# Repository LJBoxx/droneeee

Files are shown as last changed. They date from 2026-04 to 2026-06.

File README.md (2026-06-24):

# RP2350 Flight controller stack 

This repo contains the design files for a rp2350 based flight controller stack, with an [am32](https://wiki.am32.ca/development/Hardware-Design.html) based 4-in-1 modulable esc.
The esc part is split onto 3 boards : 
- top and bottoma board with logic and mosfet drivers (logic)
- middle with mosfets and power converters (powerstage)

This design allows for repairability, if you want to change the power board for a higher current one or if you have burnt it, just swap it out and solder a new board ! 

I also wanted to experiment with the newly supported rp2350 mcu on betaflight ! Madflight has an esc but I haven't seen any on a 30.5x30.5 "classic" format yet.

Thhe flight controller is quite simple and only has support for the essential to fly digital fpv with : 
- uart for elrs/radio transceiver 
- uart for video like openipc or dji
- uart for gps (additionnal too!)
- one spare i2c port (because there was room for it :v)
- power (9v 3a max, 5v 3a max and 3v3 200ma max **only use if necessary**)

Additionally, there are also some betaflight rgb headers and buzzer. Since it is an rp2350 with PIO, it should be easy to repurpose the i2c port for something else. The pinout is also similar to the madflight fc3 but not exactly the same, in /src/firmware/betaflight/picoflight/config.h you will find the exact files needed to build a firmware along precompiled binary 

At first i wanted to make an esc to work with Alice's flight controller but in the end, i started changing some parts like power converters, removing analog parts and tried to overall optimize the design. In the end it wasnt the same anymore. I also wanted to experiment with the rp2350 as no flight controller exist yet with it. One more thing was trying to make even more compact designs than before, high density layout is fun but also a pain lol.. 

## Renders :
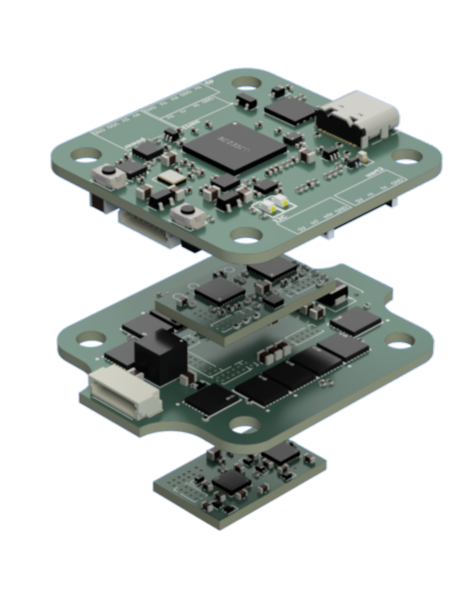
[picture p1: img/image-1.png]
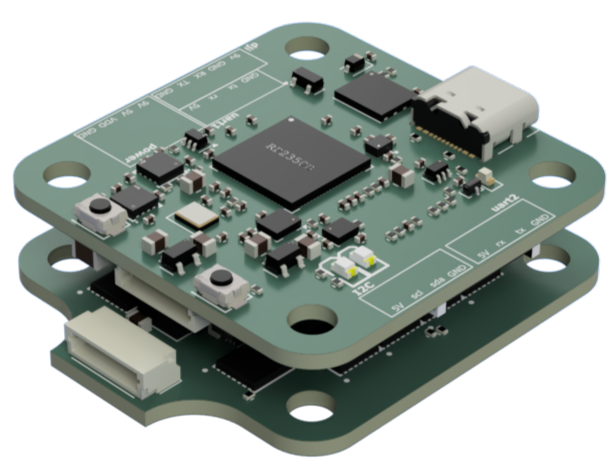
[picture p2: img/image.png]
 

## Schematics 
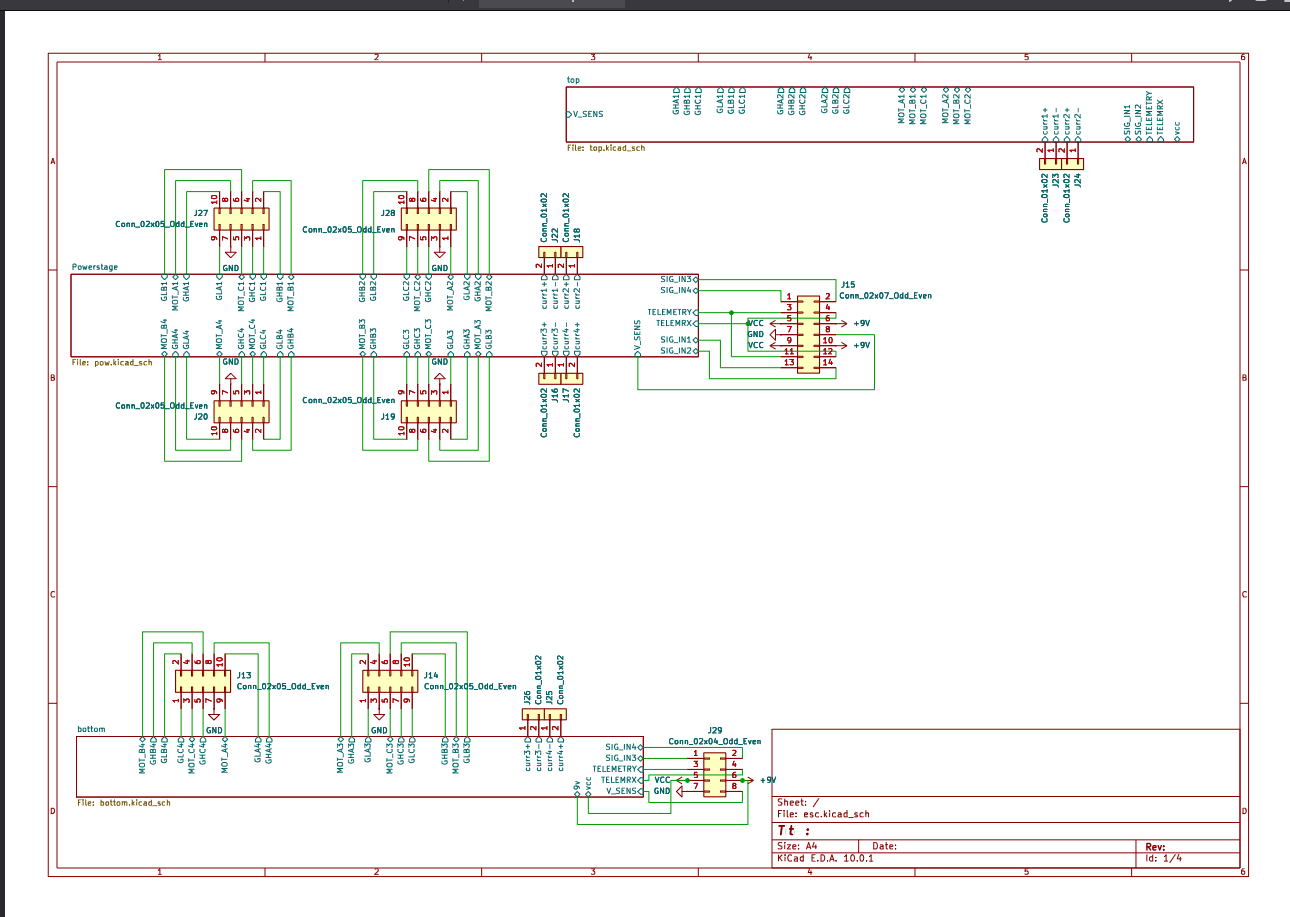
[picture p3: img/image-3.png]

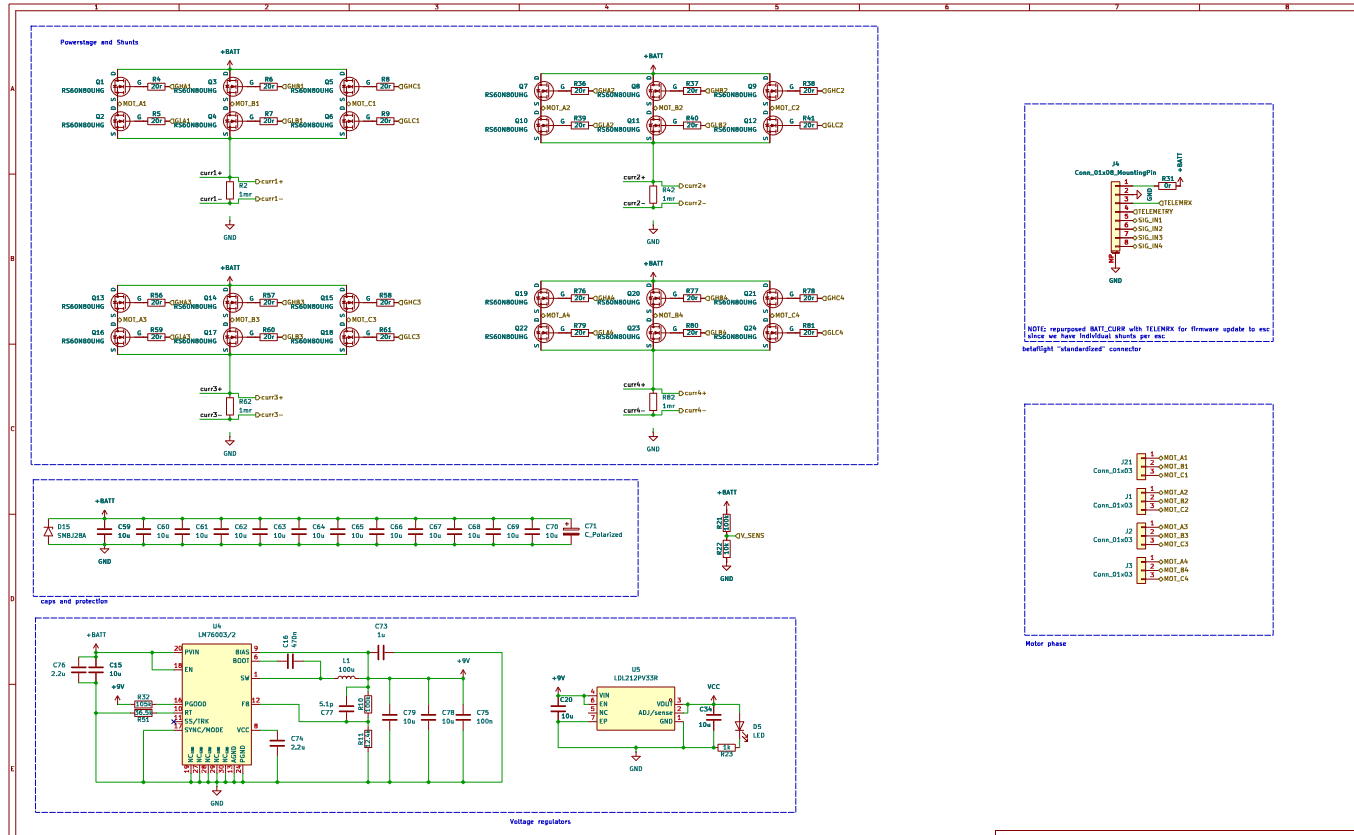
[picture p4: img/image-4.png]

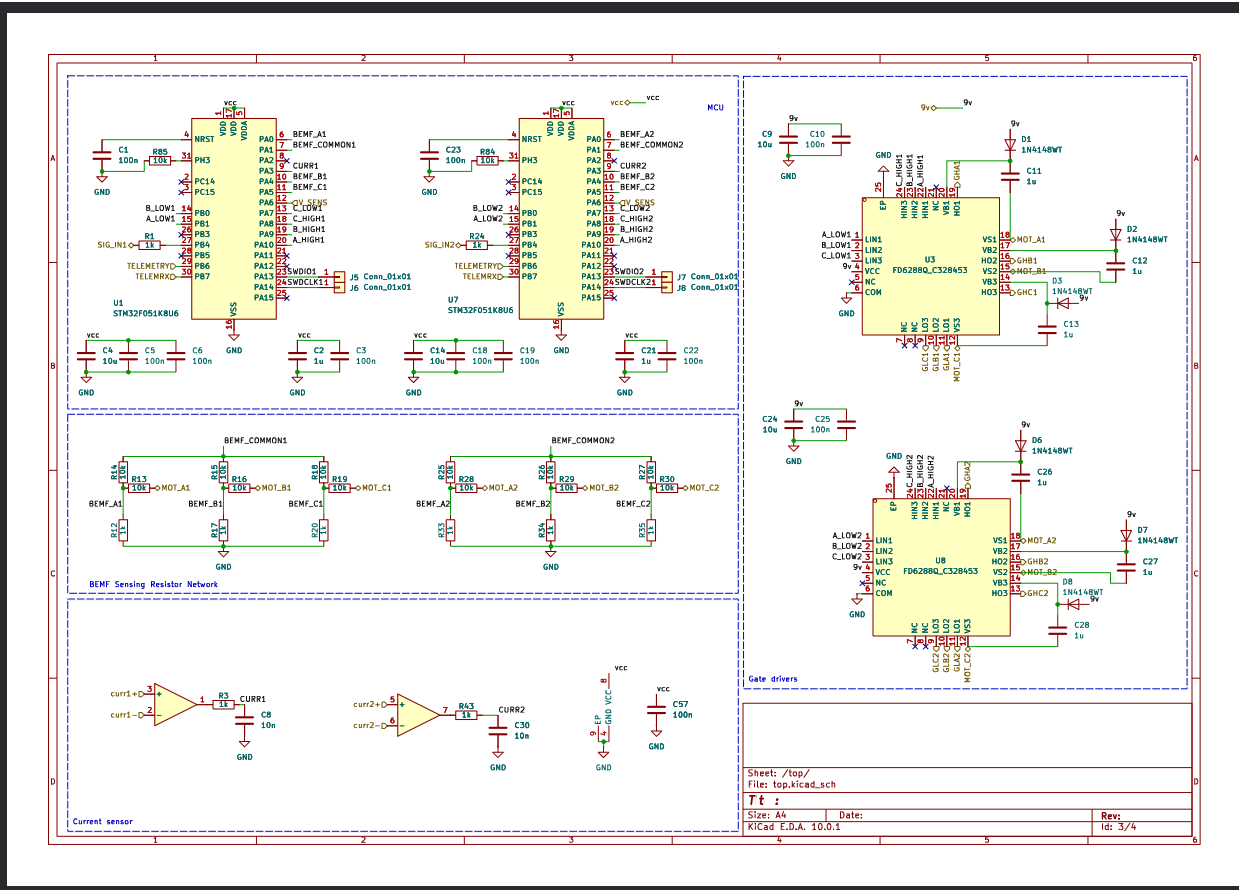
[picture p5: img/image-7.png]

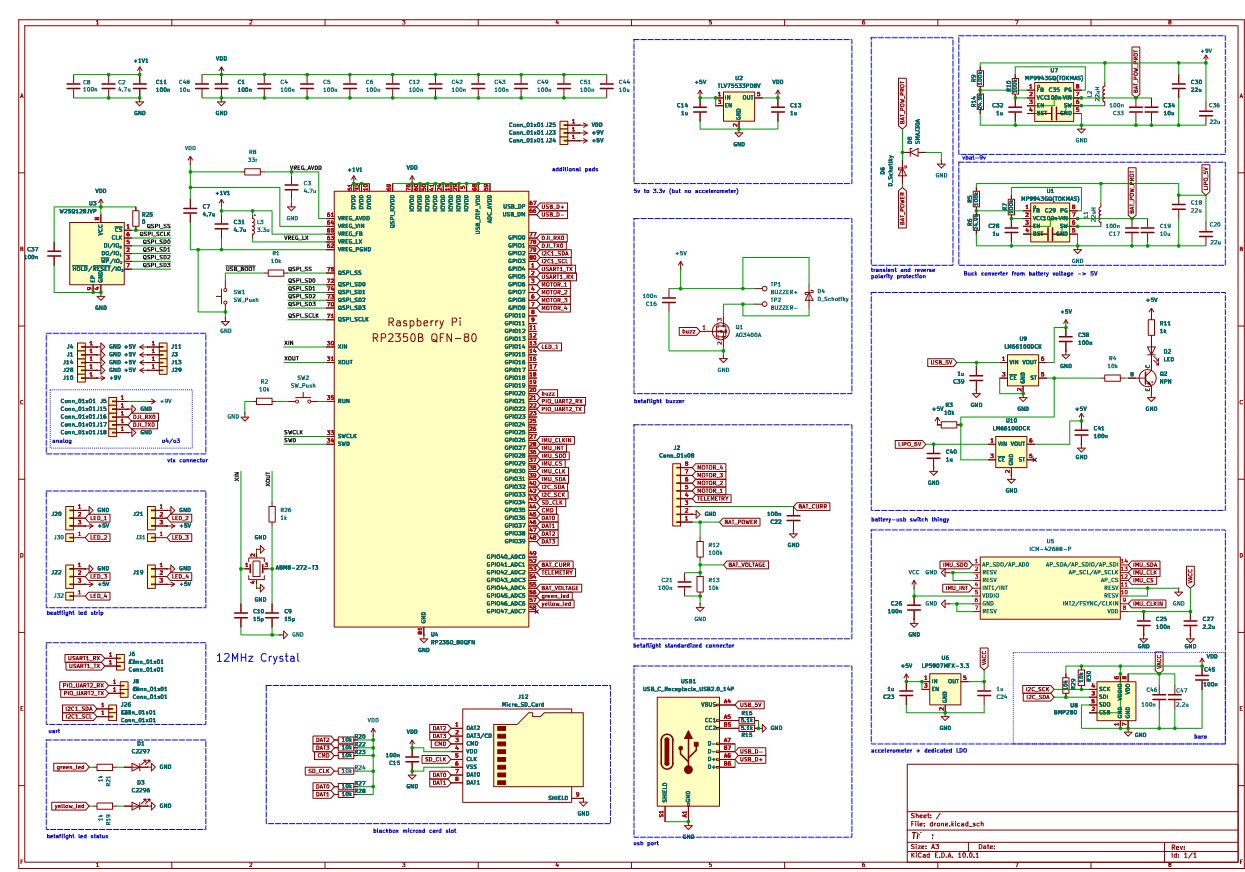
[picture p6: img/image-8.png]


# BOM 
| Name | Qty | Price  | Link | Note |
| --- | --- | --- | --- | ----- |
| Components | 1 | 110usd  | /src/bom_export_fc.xls |
| PCB | 3x5pcs  | 5usd/ea | https://jlcpcb.com/ | order each board design individually to have discounts !|
| total | | 125usd |  |shipping included

# ZINEE !!
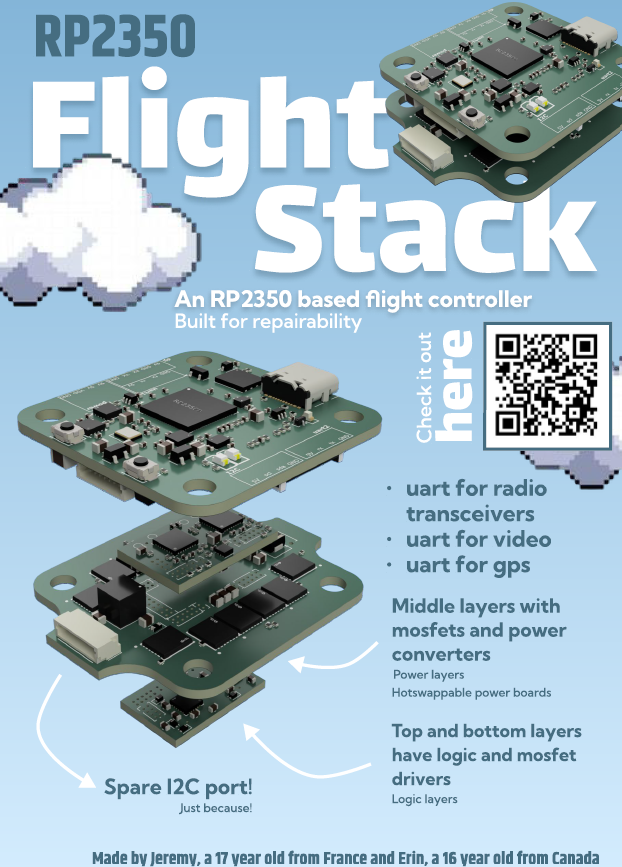
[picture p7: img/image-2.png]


# Build 
(to be done after i assemble it myself but basically soldering)

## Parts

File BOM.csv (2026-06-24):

 | Mrf# | Product Link | Unit Price(USD) | Quantity | Ext.Price(USD) | Description
1 | CL05B104KO5NNNC | https://www.lcsc.com/product-detail/C1525.html | 0.0031 | 49 | 0.31 | 100nF ±10% 16V Ceramic Capacitor X7R 0402
2 | TCC0402X6S475M6R3AT | https://www.lcsc.com/product-detail/C50767367.html | 0.0101 | 4 | 0.51 | 4.7uF X6S ±20% 6.3V 0402 Ceramic Capacitors RoHS
3 | CL05B103KB5NNNC | https://www.lcsc.com/product-detail/C15195.html | 0.0025 | 4 | 0.25 | 10nF ±10% 50V Ceramic Capacitor X7R 0402
4 | CC0402DRNPO9BN150 | https://www.lcsc.com/product-detail/C526978.html | 0.0015 | 2 | 0.15 | 15pF 50V Ceramic Capacitor NP0 0402
5 | CL10A106KO8NQNC | https://www.lcsc.com/product-detail/C962136.html | 0.0433 | 5 | 0.43 | 10uF ±10% 16V Ceramic Capacitor X5R 0603
6 | CC0805KKX7R9BB105 | https://www.lcsc.com/product-detail/C91185.html | 0.0455 | 4 | 2.28 | 1uF ±10% 50V Ceramic Capacitor X7R 0805
7 | CL05A474KA5NNNC | https://www.lcsc.com/product-detail/C92361.html | 0.0163 | 1 | 0.16 | 470nF ±10% 25V Ceramic Capacitor X5R 0402
8 | CL21A226MAYNNNE | https://www.lcsc.com/product-detail/C602037.html | 0.1138 | 4 | 1.14 | 22uF ±20% 25V Ceramic Capacitor X5R 0805
9 | CL05A225MQ5NSNC | https://www.lcsc.com/product-detail/C12530.html | 0.0078 | 3 | 0.78 | 2.2uF ±20% 6.3V Ceramic Capacitor X5R 0402
10 | GRM155B31E105KA12D | https://www.lcsc.com/product-detail/C913556.html | 0.0085 | 5 | 0.43 | 1uF ±10% 25V Ceramic Capacitor 0402
11 | CL10A105KB8NNNC | https://www.lcsc.com/product-detail/C15849.html | 0.0130 | 16 | 0.65 | 1uF ±10% 50V Ceramic Capacitor X5R 0603
12 | CC0805KKX7R9BB105 | https://www.lcsc.com/product-detail/C91185.html | 0.0455 | 2 | 2.28 | 1uF ±10% 50V Ceramic Capacitor X7R 0805
13 | CL32B106KBJNNNE | https://www.lcsc.com/product-detail/C138687.html | 0.2901 | 2 | 0.58 | 10uF ±10% 50V Ceramic Capacitor X7R 1210
14 | CL10A225KB8NNNC | https://www.lcsc.com/product-detail/C913904.html | 0.0400 | 1 | 0.40 | 2.2uF ±10% 50V Ceramic Capacitor X5R 0603
15 | GRM21BR61E106MA73L | https://www.lcsc.com/product-detail/C391262.html | 0.0326 | 23 | 1.30 | 10uF ±20% 25V Ceramic Capacitor X5R 0805
16 | CC0402DRNPO9BN5R1 | https://www.lcsc.com/product-detail/C541354.html | 0.0016 | 1 | 0.16 | 5.1pF 50V Ceramic Capacitor NP0 0402
17 | KT-0805G | https://www.lcsc.com/product-detail/C2297.html | 0.0163 | 1 | 0.82 | Emerald Green 525nm LED Indication - Discrete 2.6V~3.1V 0805
18 | F.0603.00026/P2-0603B1TS2-06T-001 | https://www.lcsc.com/product-detail/C7496819.html | 0.0044 | 1 | 0.44 | Blue 462nm LED Indication - Discrete 2.5V~2.9V 0603
19 | KT-0603R | https://www.lcsc.com/product-detail/C2286.html | 0.0073 | 1 | 0.73 | Red 645nm LED Indication - Discrete 2.4V 0603
20 | KT-0805Y | https://www.lcsc.com/product-detail/C2296.html | 0.0123 | 1 | 0.62 | Yellow 596nm LED Indication - Discrete 1.8V~2.4V 0805
21 | 1SS404 | https://www.lcsc.com/product-detail/C2100.html | 0.0360 | 1 | 0.72 | Diode 20V 300mA Surface Mount SOD-323
22 | SS210 | https://www.lcsc.com/product-detail/C14996.html | 0.0291 | 1 | 1.46 | Diode 100V 2A Surface Mount SMA(DO-214AC)
23 | SMAJ30A | https://www.lcsc.com/product-detail/C10767.html | 0.0699 | 1 | 0.70 | 48.4VC Clamp 8.3A@10/1000us Ipp TVS DIODE DO-214AC(SMA)
24 | SM08B-SRSS-TB(LF)(SN) | https://www.lcsc.com/product-detail/C160407.html | 0.3186 | 2 | 1.59 | Connector Header 8 position 1mm Pitch 1A Surface Mount, Right Angle -25℃~+85℃
25 | 472192001 | https://www.lcsc.com/product-detail/C164170.html | 0.7566 | 1 | 0.76 | Micro SD card (TF card) Connector and Ejector Hinged Lid Surface Mount
26 | HX PZ1.0-2x5P ZZ | https://www.lcsc.com/product-detail/C22438182.html | 0.0789 | 6 | 0.79 | Pin Header 10 Position 1mm Pitch Dual Row Through Hole -40℃~+105℃
27 | GPCA101-0502A001C1AA | https://www.lcsc.com/product-detail/C5138889.html | 0.1754 | 8 | 1.75 | Pin Header 5 Position 1mm Pitch Single Row Through Hole -40℃~+105℃
28 | FC-ALX 5050D-150MT | https://www.lcsc.com/product-detail/C5370912.html | 0.8411 | 1 | 0.84 | 5.5A 15uH ±20% 6.5A 45mΩ Molded Inductor SMD,5.1x5.3mm Fixed Inductors RoHS
29 | CYN5040-22UH | https://www.lcsc.com/product-detail/C2879700.html | 0.1140 | 2 | 0.57 | 1.4A 22uH ±20% 129mΩ 1.8A SMD,5x5mm Fixed Inductors RoHS
30 | AOTA-B201610S3R3-101-T | https://www.lcsc.com/product-detail/C42411119.html | 0.2838 | 1 | 1.42 | 2.1A 3.3uH 115mΩ 2.4A Molded Inductor 0806 Fixed Inductors RoHS
31 | AO3400A | https://www.lcsc.com/product-detail/C20917.html | 0.0846 | 1 | 0.42 | N-Channel 30V Surface Mount SOT-23-3L
32 | MMBT3904TT1G | https://www.lcsc.com/product-detail/C242260.html | 0.0264 | 1 | 0.53 | Bipolar (BJT) Transistor NPN 40V 200mA 300MHz 200mW Surface Mount SOT-416
33 | RT0402BRD0710KL | https://www.lcsc.com/product-detail/C190095.html | 0.0207 | 42 | 1.04 | 62.5mW 10kΩ 50V Thin Film Resistor ±25ppm/℃ ±0.1% 0402 Chip Resistor - Surface Mount RoHS
34 | ERA2AEB104X | https://www.lcsc.com/product-detail/C445619.html | 0.0701 | 7 | 0.70 | 100kΩ ±0.1% 63mW 0402 Thin Film Resistor AEC-Q200
35 | RT0402BRD0724K9L | https://www.lcsc.com/product-detail/C852664.html | 0.0274 | 2 | 0.55 | 24.9kΩ 63mW 50V Thin Film Resistor ±25ppm/℃ ±0.1% 0402 Chip Resistor - Surface Mount RoHS
36 | ERJPA2J330X | https://www.lcsc.com/product-detail/C427200.html | 0.0257 | 1 | 0.51 | 33Ω ±5% 250mW 0402 Thick Film Resistor AEC-Q200
37 | FRC0402F1053TS | https://www.lcsc.com/product-detail/C2933067.html | 0.0015 | 1 | 0.15 | 105kΩ ±1% 62.5mW 0402 Thick Film Resistor
38 | RK73H1ET3652F-CN | https://www.lcsc.com/product-detail/C42396638.html | 0.0014 | 1 | 0.14 | 62.5mW 36.5kΩ Thick Film Resistor ±1% 0402 Chip Resistor - Surface Mount RoHS
39 | ERA2AEB1242X | https://www.lcsc.com/product-detail/C490814.html | 0.0933 | 1 | 0.47 | 12.4kΩ ±0.1% 63mW 0402 Thin Film Resistor AEC-Q200
40 | ERA2AEB102X | https://www.lcsc.com/product-detail/C445596.html | 0.1037 | 25 | 2.59 | 1kΩ ±0.1% 63mW 0402 Thin Film Resistor AEC-Q200
41 | PMR25HZPJV1L0 | https://www.lcsc.com/product-detail/C4173351.html | 0.6267 | 4 | 2.51 | 1W 1mΩ ±100ppm/℃ ±5% 1210 Chip Resistor - Surface Mount RoHS
42 | FRC0402F20R0TS | https://www.lcsc.com/product-detail/C2909334.html | 0.0015 | 24 | 0.15 | 20Ω ±1% 62.5mW 0402 Thick Film Resistor
43 | 0402WGF5101TCE | https://www.lcsc.com/product-detail/C25905.html | 0.0009 | 2 | 0.09 | 5.1kΩ ±1% 62.5mW 0402 Thick Film Resistor
44 | TS-1088-AR02016 | https://www.lcsc.com/product-detail/C720477.html | 0.0530 | 2 | 0.53 | Tactile Switch SPST 160gf 2mm SMD (SMT) Tab 4mm x 3mm Surface Mount
45 | STM32F051K8U6 | https://www.lcsc.com/product-detail/C72339.html | 1.8196 | 4 | 7.28 | ARM Cortex-M0 32 Bit 48MHz 27 UFQFPN-32(5x5) Microcontrollers RoHS
46 | MP9943GQ(TOKMAS) | https://www.lcsc.com/product-detail/C51889390.html | 1.3803 | 2 | 2.76 | Step-down type 350kHz~470kHz Adjustable 0V~24V 3A QFN-8(3x3) Voltage Regulators - DC DC Switching Regulators RoHS
47 | TLV75533PDBVR | https://www.lcsc.com/product-detail/C404027.html | 0.1459 | 1 | 0.73 | 3.3V Positive Fixed SOT-23-5 Voltage Regulators - Linear, Low Drop Out (LDO) Regulators RoHS
48 | W25Q128JVPIM TR | https://www.lcsc.com/product-detail/C2441427.html | 3.0088 | 1 | 3.01 | FLASH - NOR Memory IC 128Mbit SPI 133MHz WSON-8-EP(5x6)
49 | RP2354B | https://www.lcsc.com/product-detail/C39843328.html | 1.5739 | 1 | 1.57 | 48 QFN-80-EP(10x10) Microcontrollers RoHS
50 | ICM-42688-P | https://www.lcsc.com/product-detail/C1850418.html | 20.2811 | 1 | 20.28 | High Precision 6-Axis MEMS MotionTracking Device
51 | LP5907MFX-3.3/NOPB | https://www.lcsc.com/product-detail/C80670.html | 0.1369 | 1 | 0.68 | Linear Voltage Regulator IC Positive Fixed 1 Output 250mA SOT-23-5
52 | LM66100DCKR | https://www.lcsc.com/product-detail/C2869734.html | 0.2655 | 2 | 1.33 | 95mΩ 1 SC-70-6 OR Controllers, Ideal Diodes RoHS
53 | TYPE-C 16PIN 2MD(073) | https://www.lcsc.com/product-detail/C2765186.html | 0.0707 | 1 | 1.41 | USB-C (USB TYPE-C) Receptacle Connector 16 Position Surface Mount, Right Angle
54 | FD6288Q | https://www.lcsc.com/product-detail/C328453.html | 0.8639 | 4 | 3.46 | Three Phase Gate Driver IC MOSFET IGBT QFN-24-EP(4x4)
55 | RS60N80UHG | https://www.lcsc.com/product-detail/C51904706.html | 0.1957 | 24 | 4.89 | 60V 80A 3.6V 78W 4.2mΩ@10V 1 N-channel PDFN-8(5x6) Single FETs, MOSFETs RoHS
56 | LDL212PV33R | https://www.lcsc.com/product-detail/C2969892.html | 0.5797 | 1 | 0.58 | 3.3V Positive Fixed DFN-6(2x2) Voltage Regulators - Linear, Low Drop Out (LDO) Regulators RoHS
57 | SMBJ28A | https://www.lcsc.com/product-detail/C178227.html | 0.1082 | 1 | 0.54 | 45.4VC Clamp 13.3A@10/1000us Ipp TVS DIODE DO-214AA
58 | INA2180A1IDSGR | https://www.lcsc.com/product-detail/C2873353.html | 0.3972 | 2 | 0.79 | 2 25uV -200mV~26V 2V/us 350kHz 100dB 100nA 355uA 20V/V WSON-8(2x2) Instrumentation, Op Amps, Buffer Amps RoHS
59 | LM76003RNPR | https://www.lcsc.com/product-detail/C470958.html | 2.2912 | 1 | 2.29 | 2.2MHz Step-down type Adjustable 1V~57V 3.5A WQFN-30-EP(4x6) Voltage Regulators - DC DC Switching Regulators RoHS
60 | 1N4148WT | https://www.lcsc.com/product-detail/C917006.html | 0.0079 | 12 | 0.40 | Diode Independent 75V 150mA Surface Mount SOD-523
61 | ABM8-272-T3 | https://www.lcsc.com/product-detail/C20625731.html | 0.2956 | 1 | 1.48 | ±30ppm 10pF ±30ppm SMD3225-4P Crystals RoHS
62 | BMP280 | https://www.lcsc.com/product-detail/C83291.html | 6.9336 | 1 | 6.93 | 30Kpa~1.1bar LGA-8(2x2.5) Pressure Sensors, Transducers RoHS
63 | UHW1H102MHD | https://www.lcsc.com/product-detail/C250864.html | 0.9688 | 1 | 0.97 | 1000uF 50V Aluminum Electrolytic Capacitors Through Hole,D12.5xL31.5mm 10000hrs@105℃
64 | PCB | https://jlcpcb.com |  | 5 | 2.00 | Flight controller pcb
65 | PCB | https://jlcpcb.com |  | 5 | 2.00 | esc logic pcb
66 | PCB | https://jlcpcb.com |  | 5 | 2.00 | esc powerstage pcb
Total |  |  |  |  | $102.78

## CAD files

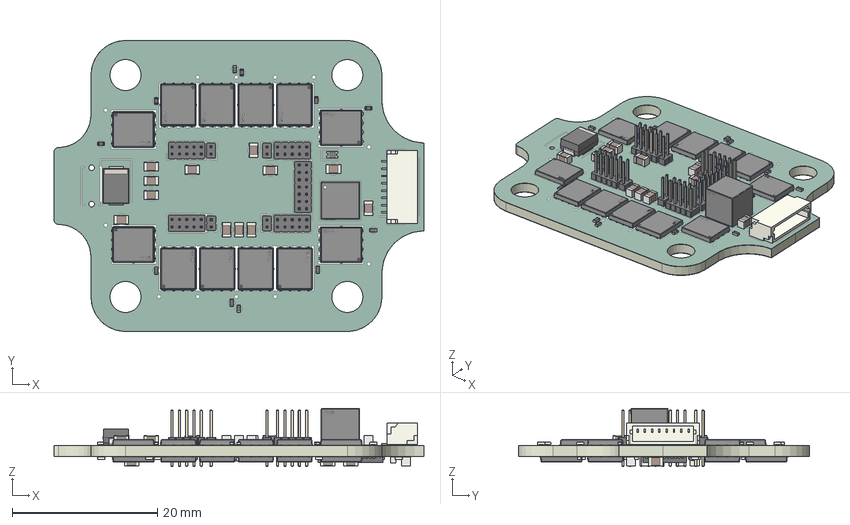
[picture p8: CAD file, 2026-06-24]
3d/power.step
50.9 x 40.0 x 8.00 mm
PinHeader_1x02_P1.00mm_Vertical x 4
DFN-8_L5.8-W4.9-P1.27-LS6.0-BL-1 x 24
C_0805_2012Metric x 17
R_0402_1005Metric x 32
PinHeader_2x07_P1.00mm_Vertical
D_SMB
D_0603_1608Metric
PinHeader_2x05_P1.00mm_Vertical x 4
JST_SH_SM08B-SRSS-TB_1x08-1MP_P1.00mm_Horizontal
IND-SMD_L5.3-W5.1_FC-ALX5050D
C_0402_1005Metric x 5
R_1210_3225Metric x 4
WQFN-30_L6.0-W4.0-H0.8-P0.50-BL-EP
DFN-6_L2.0-W2.0-P0.50-BL-EP1.45
C_0603_1608Metric
esc_silkscreen x 2
esc_soldermask x 2
esc_PCB

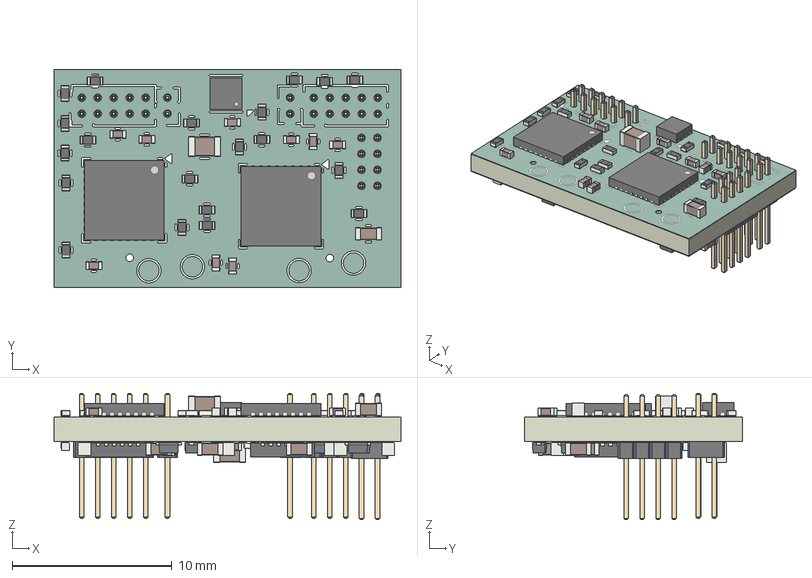
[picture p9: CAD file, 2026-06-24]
hardware/esc/logic.step
21.7 x 13.6 x 7.88 mm
R_0402_1005Metric x 24
C_0402_1005Metric x 13
PinHeader_1x02_P1.00mm_Vertical x 2
QFN-32-1EP_5x5mm_P0.5mm_EP3.45x3.45mm x 2
C_0805_2012Metric x 2
PinHeader_2x05_P1.00mm_Vertical x 2
C_0603_1608Metric x 11
WSON-8-1EP_2x2mm_P0.5mm_EP0.9x1.6mm
D_SOD-523 x 6
QFN-24_L4.0-W4.0-H0.9-P0.50 x 2
PinHeader_2x04_P1.00mm_Vertical
esc_silkscreen x 2
esc_soldermask x 2
esc_PCB

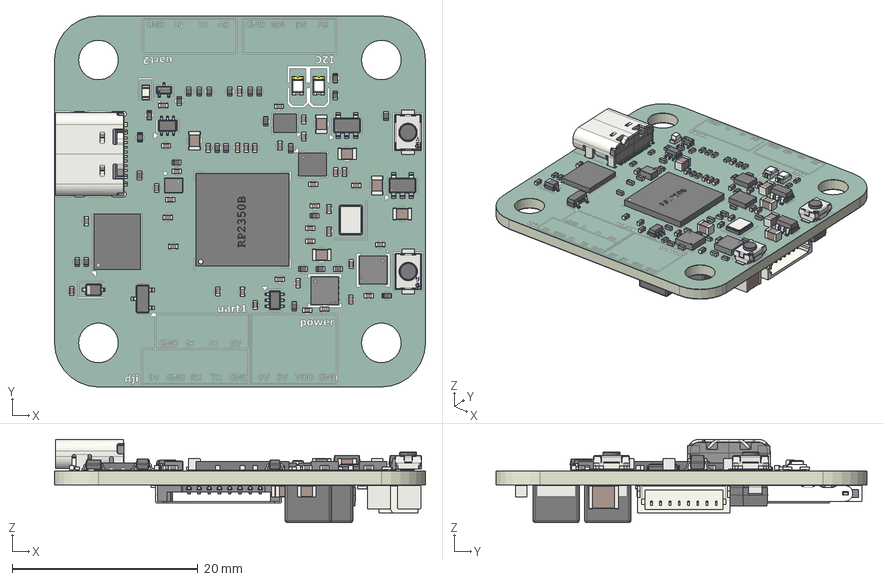
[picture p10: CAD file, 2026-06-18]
hardware/fc/fc.step
40.0 x 40.0 x 8.99 mm
R_0402_1005Metric x 28
C_0402_1005Metric x 38
IND-SMD_L2.0-W1.6_AOTA-B201610S3R3-101-T
SOT-23-5 x 2
C_0805_2012Metric x 10
LED0805-RD x 2
Bosch_LGA-8_2x2.5mm_P0.65mm_ClockwisePinNumbering
RP2350_QFN80
D_SOD-323
SW-SMD_L3.9-W2.9-H2.0-LS4.8 x 2
SOT-363_SC-70-6 x 2
WSON-8-1EP_6x5mm_P1.27mm_EP3.4x4.3mm
QFN-8_L3.0-W3.0-P0.65-BL x 2
SC-75-3_L1.6-W0.8-H0.9-LS1.6-P1.0
SOT-23
LED_0603_1608Metric
USB_C_Receptacle_GCT_USB4105-xx-A_16P_TopMnt_Horizontal
Bosch_LGA-14_3x2.5mm_P0.5mm
Crystal_SMD_3225-4Pin_3.2x2.5mm
C_1210_3225Metric x 2
L_Cenker_CKCS5040 x 2
TF-SMD_472192001
JST_SH_SM08B-SRSS-TB_1x08-1MP_P1.00mm_Horizontal
D_SMA x 2
drone_silkscreen x 2
drone_soldermask x 2
drone_PCB

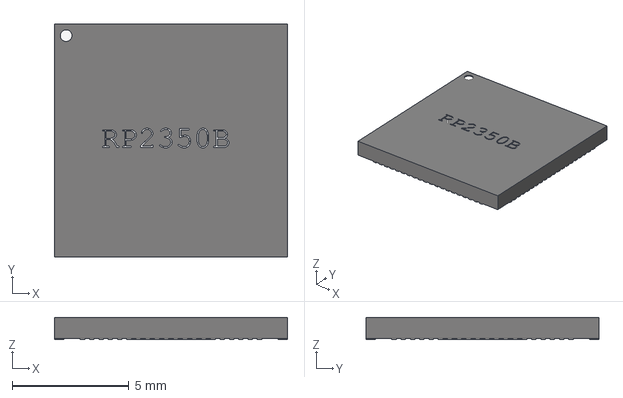
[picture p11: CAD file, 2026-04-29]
hardware/fc/RP2350_QFN80.step
10.0 x 10.0 x 0.95 mm

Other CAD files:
3d/assembly.f3z

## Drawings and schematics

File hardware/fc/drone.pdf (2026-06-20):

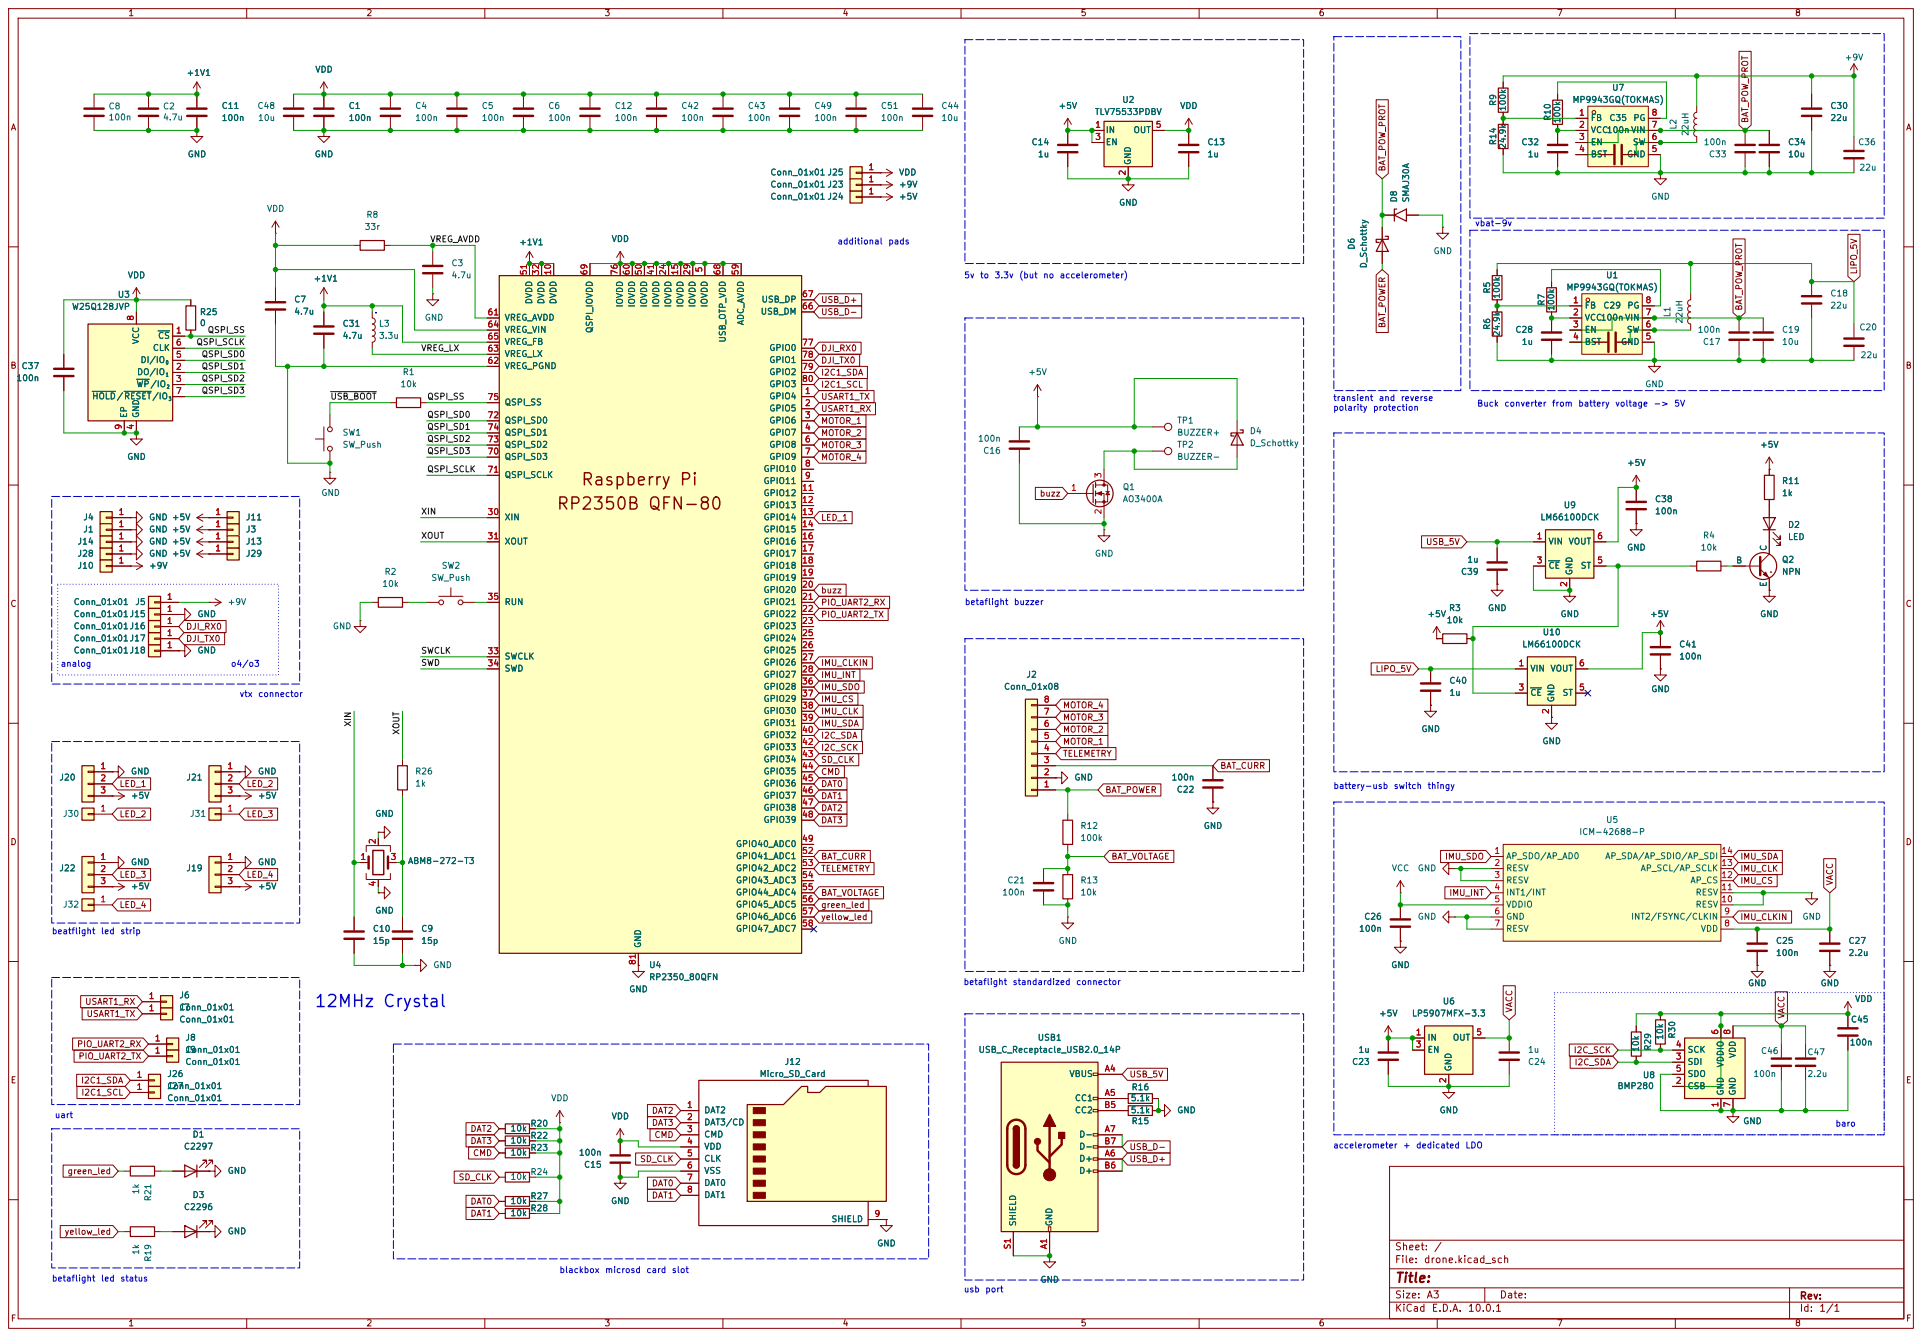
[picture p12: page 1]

5 GPIO8 6 GPIO9 7 GPIO10 8 GPIO11 9 DVDD 10 GPIO12 11 GPIO13 12 GPIO14 13 GPIO15 14 IOVDD 15 GPIO16 16 GPIO17 17 GPIO18 18 GPIO19 19 GPIO20 20 GPIO21 21 GPIO22 22 GPIO23 23 IOVDD 24 GPIO24 25 GPIO25 26 GPIO26 27 GPIO27 28 IOVDD 29

VCC 2 | 7 PG

4 DI/IO0 5 CLK 6 HOLD/RESET/IO3 7 VCC

vtx connector uart betaflight led status

betaflight standardized connector 12MHz Crystal

blackbox microsd card slot

Size: A3 | Rev: | F Date:
KiCad E.D.A. 10.0.1 | Id: 1/1

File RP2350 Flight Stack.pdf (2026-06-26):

# RP2350 Flight

# Stack

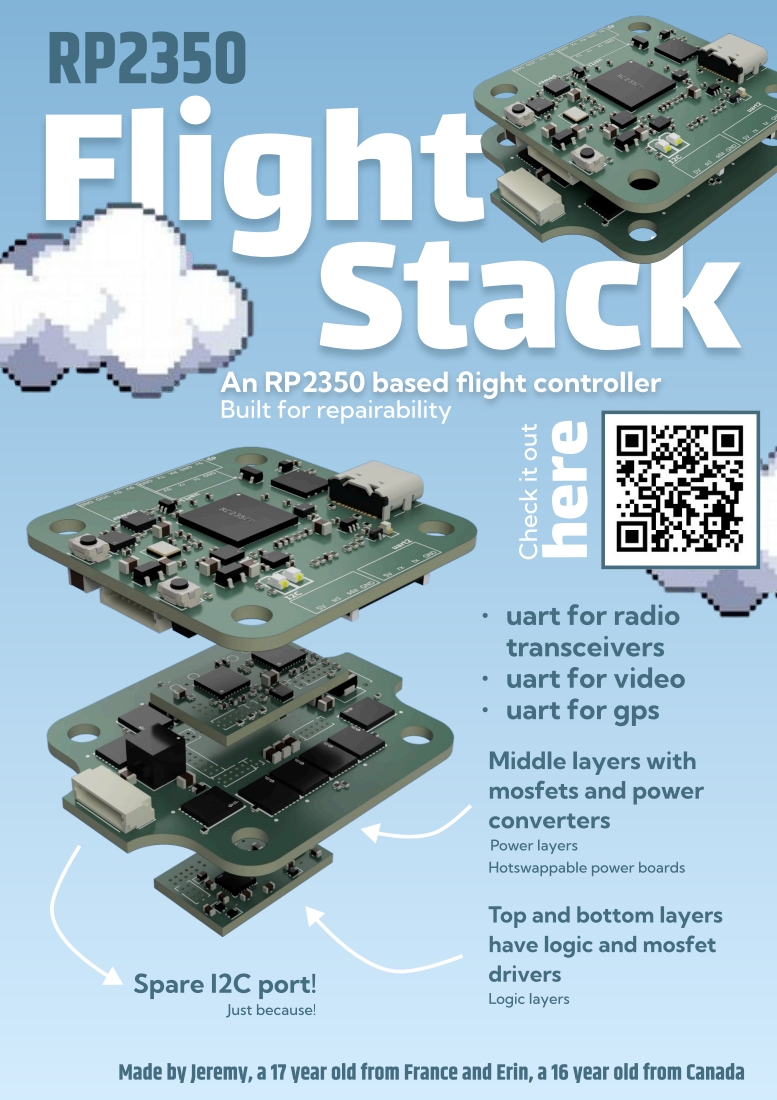
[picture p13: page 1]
here; Spare I2C port!; Just because!; Logic layers

An RP2350 based flight controller
Built for repairability

Check it out

uart for radio
transceivers
uart for video
uart for gps

Middle layers with
mosfets and power
converters

Power layers
Hotswappable power boards

Top and bottom layers
have logic and mosfet
drivers

Made by Jeremy, a 17 year old from France and Erin, a 16 year old from Canada

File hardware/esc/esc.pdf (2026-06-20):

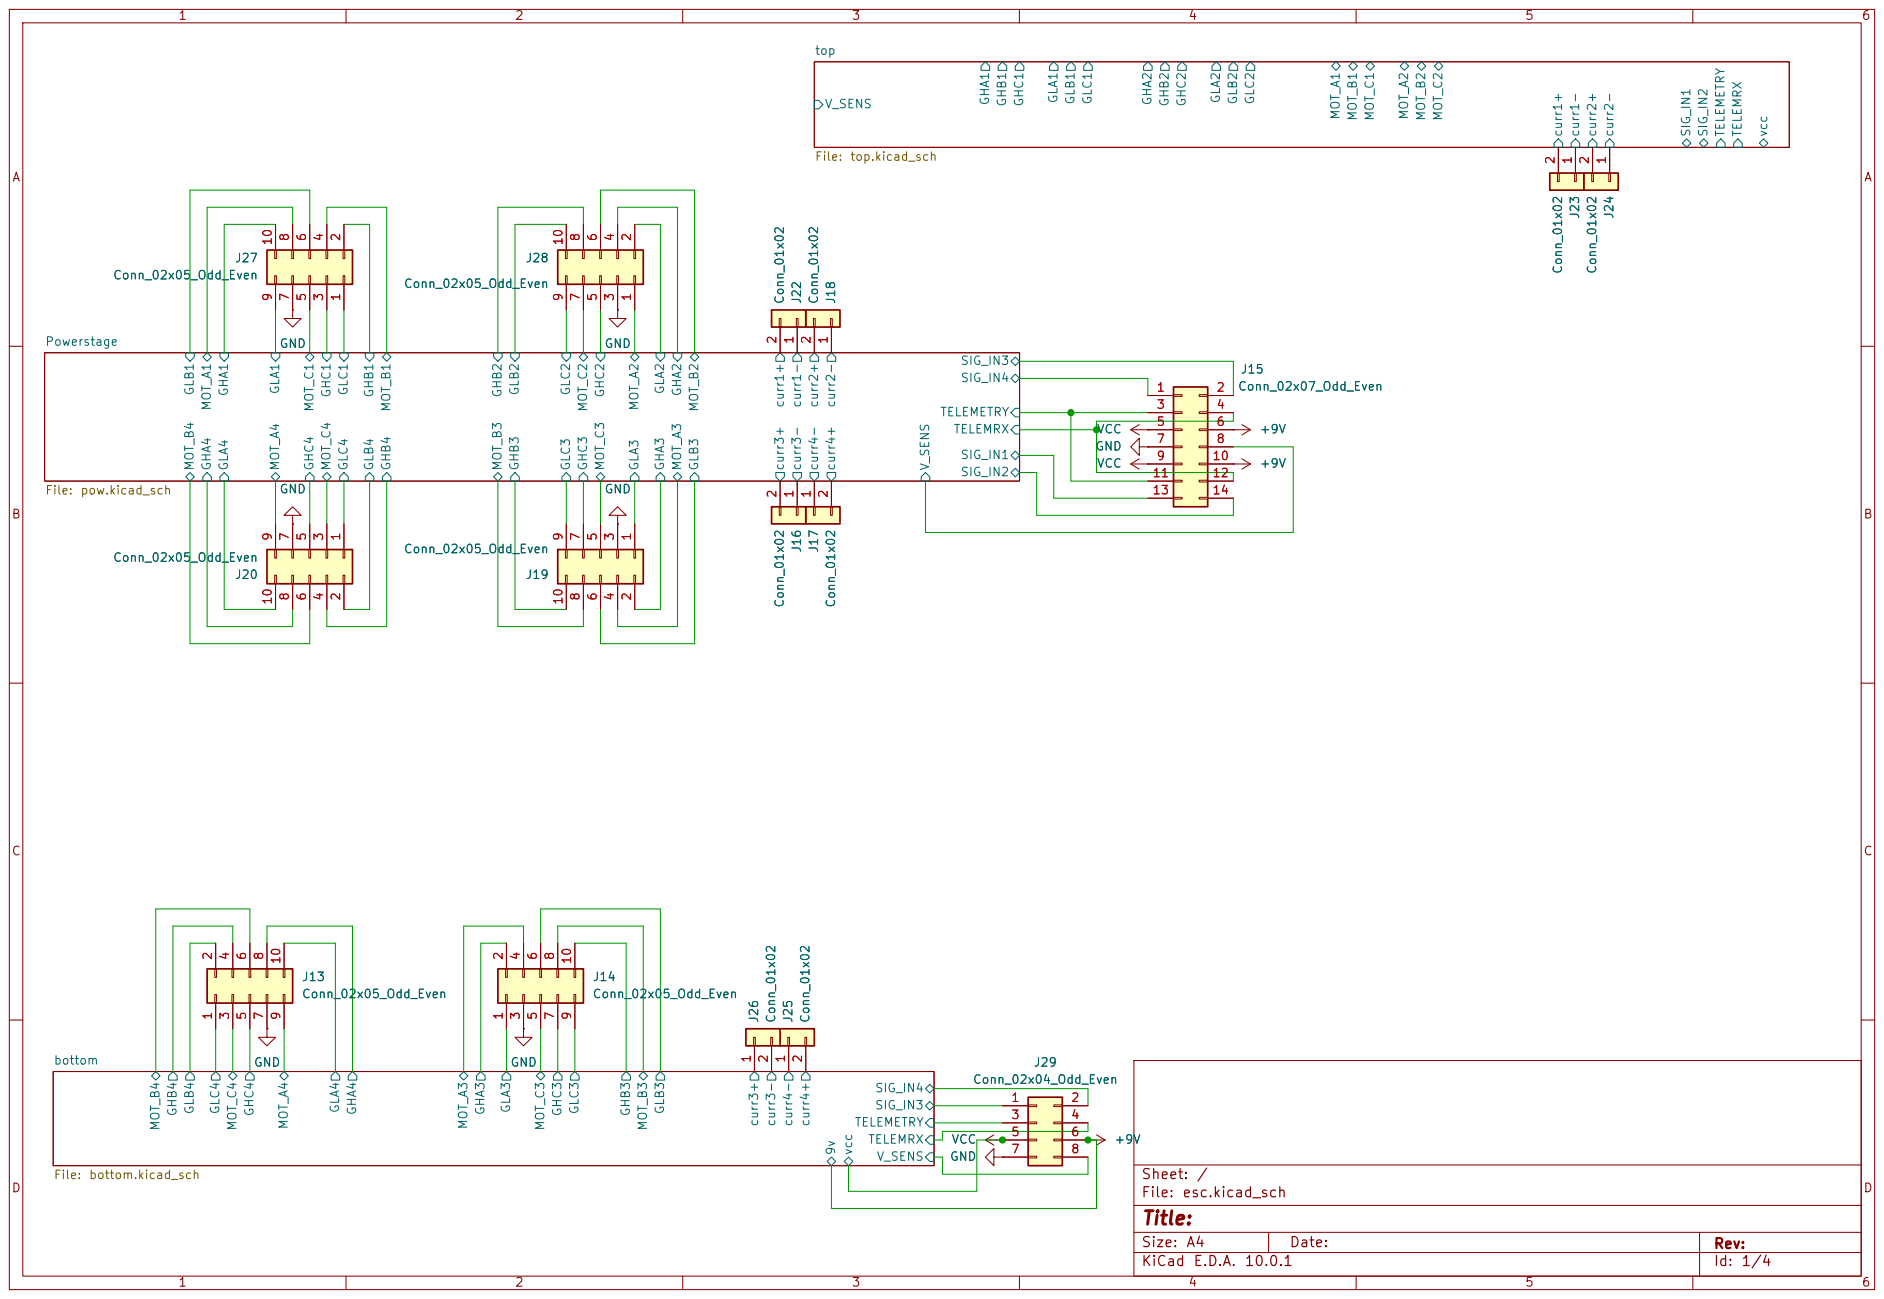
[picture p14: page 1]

Size: A4 | Rev:
KiCad E.D.A. 10.0.1 | Id: 1/4

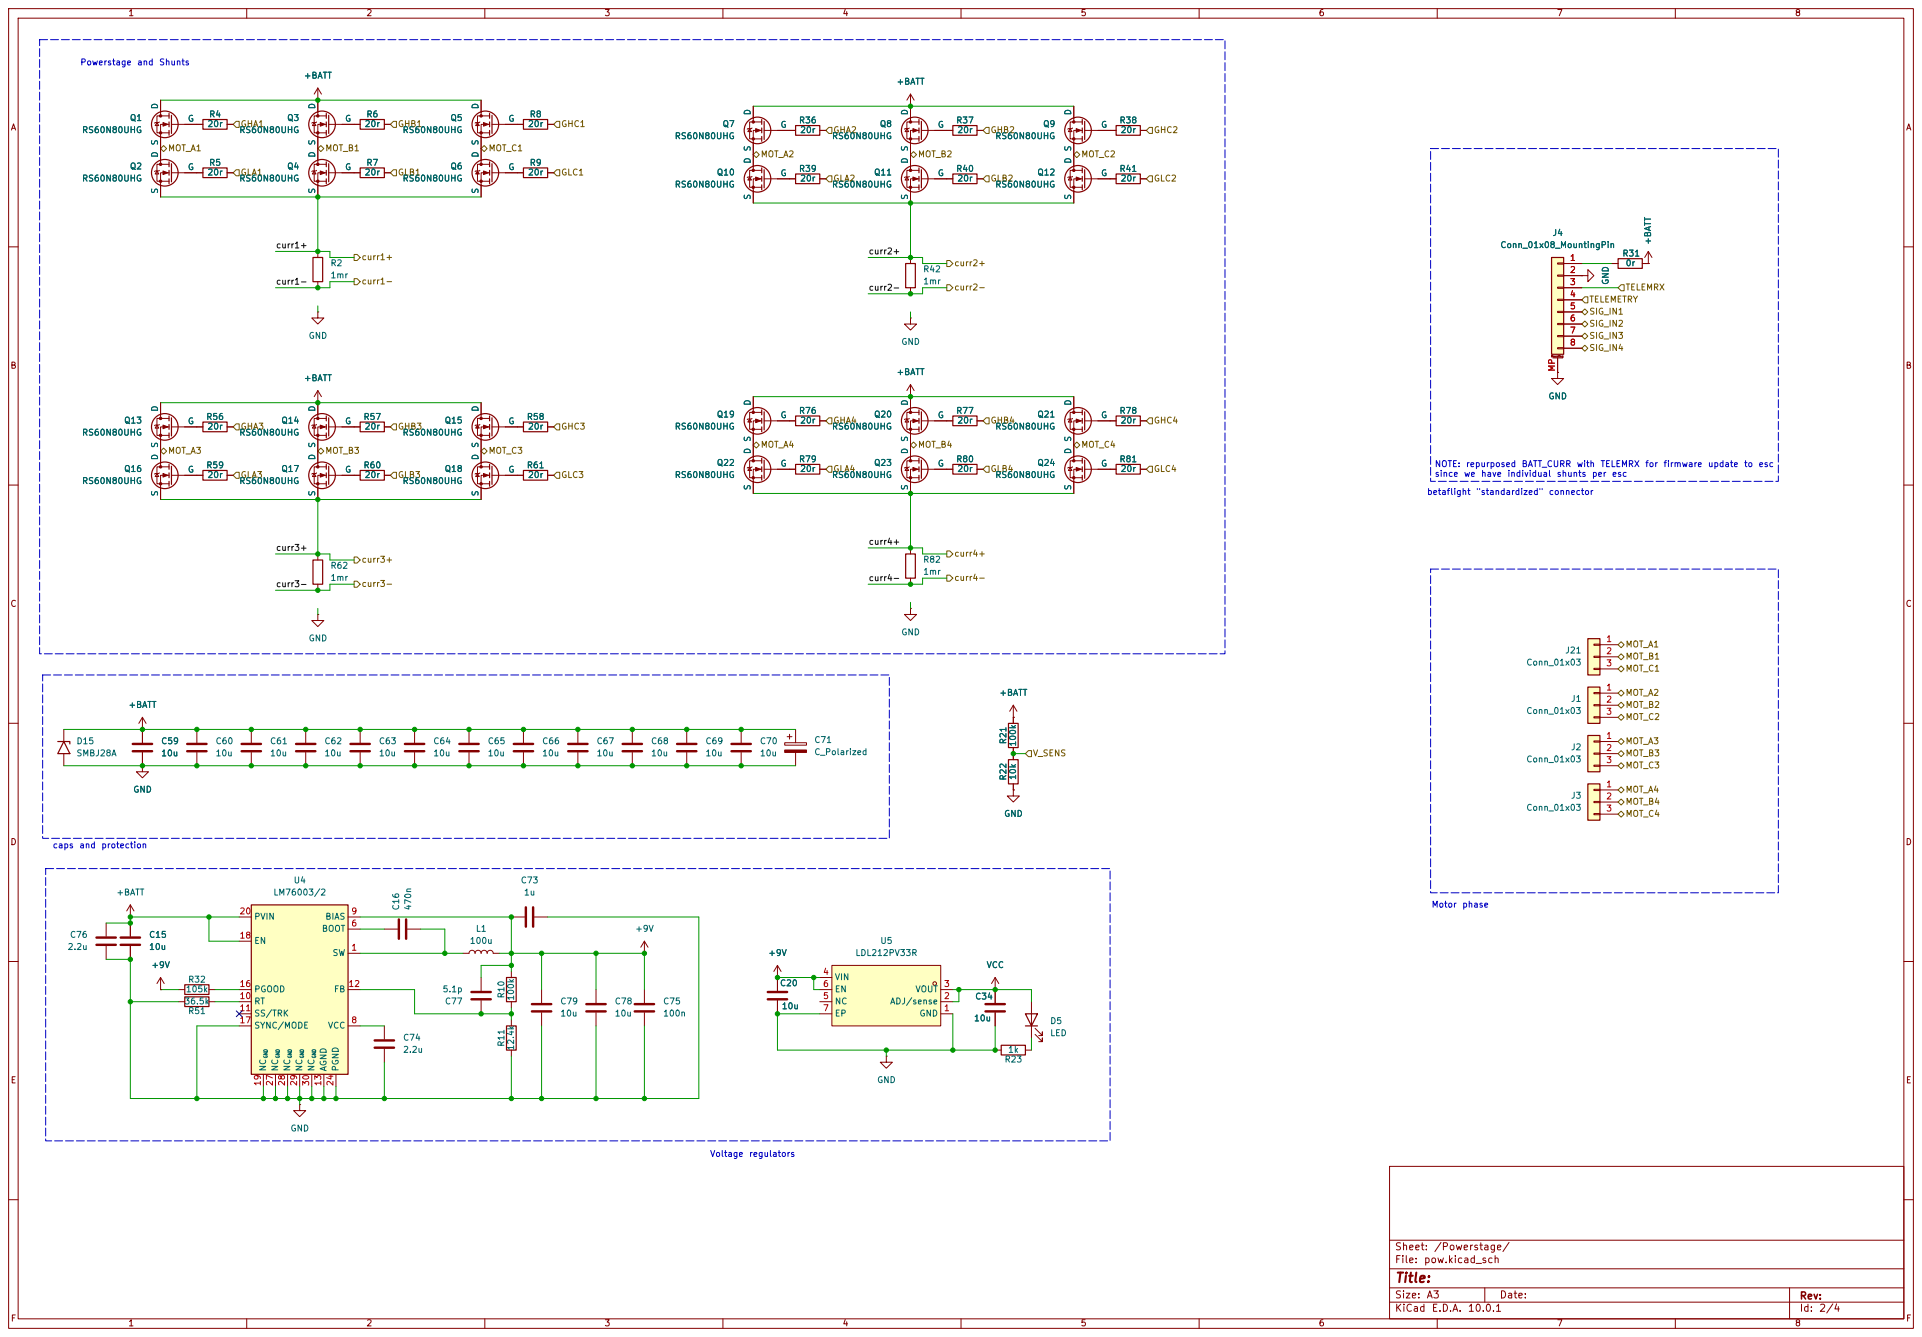
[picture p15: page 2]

betaflight "standardized" connector NOTE: repurposed BATT_CURR with TELEMRX for firmware update to esc
since we have individual shunts per esc

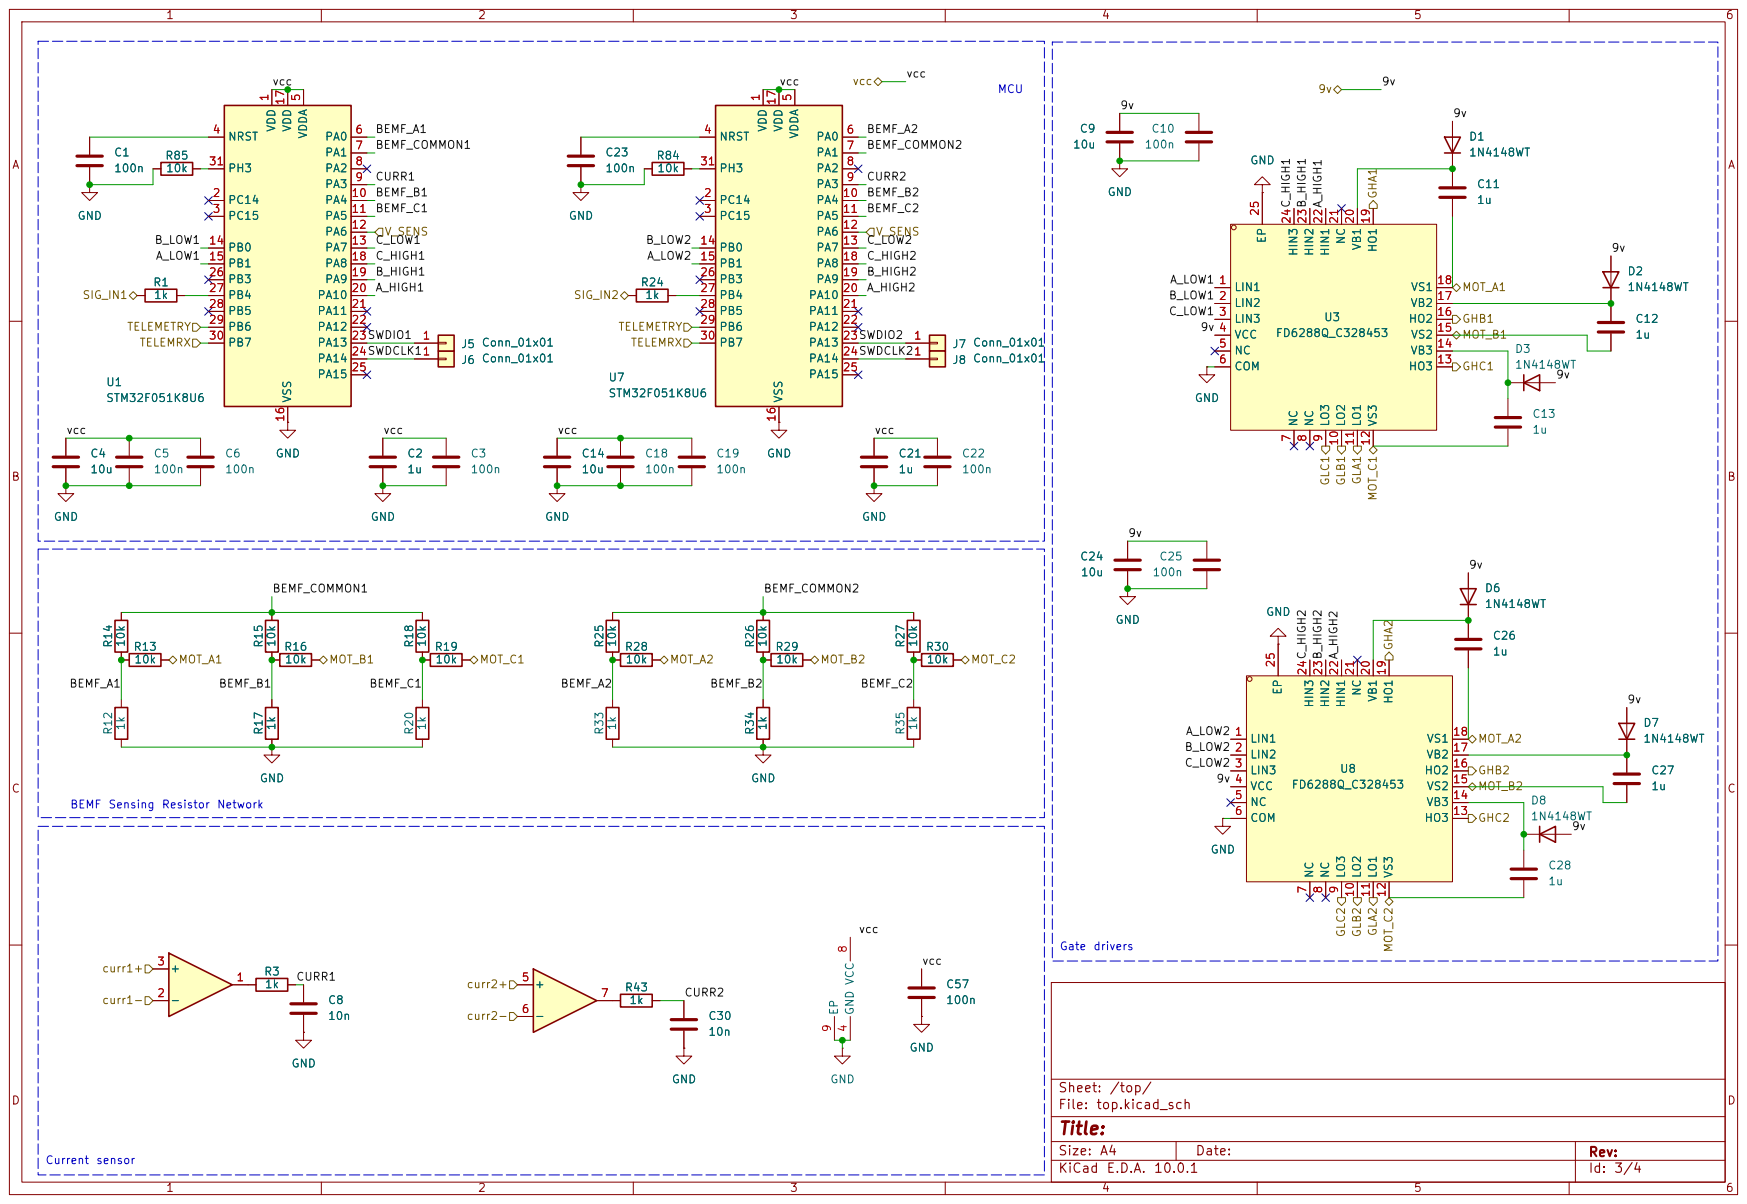
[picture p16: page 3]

1 PC14 2 PC15 3 NRST 4 VDDA 5 PA0 6 PA1 7 PA2 8 PA3 9 PA4 10 PA5 11 PA6 12 PA7 13 PB0 14 PB1 15 VSS 16 VDD 17 PA8 18 PA9 19 PA10 20 PA11 21 PA12 22 PA13 23 PA14 24 PA15 25 PB3 26 PB4 27 PB5 28 PB6 29 PB7 30 PH3 31 U1

1 PC14 2 PC15 3 NRST 4 VDDA 5 PA0 6 PA1 7 PA2 8 PA3 9 PA4 10 PA5 11 PA6 12 PA7 13 PB0 14 PB1 15 VSS 16 VDD 17 PA8 18 PA9 19 PA10 20 PA11 21 PA12 22 PA13 23 PA14 24 PA15 25 PB3 26 PB4 27 PB5 28 PB6 29 PB7 30 PH3 31 C1

1 PC14 2 PC15 3 NRST 4 VDDA 5 PA0 6 PA1 7 PA2 8 PA3 9 PA4 10 PA5 11 PA6 12 PA7 13 PB0 14 PB1 15 VSS 16 VDD 17 PA8 18 PA9 19 PA10 20 PA11 21 PA12 22 PA13 23 PA14 24 PA15 25 PB3 26 PB4 27 PB5 28 PB6 29 PB7 30 PH3 31 U7

1 PC14 2 PC15 3 NRST 4 VDDA 5 PA0 6 PA1 7 PA2 8 PA3 9 PA4 10 PA5 11 PA6 12 PA7 13 PB0 14 PB1 15 VSS 16 VDD 17 PA8 18 PA9 19 PA10 20 PA11 21 PA12 22 PA13 23 PA14 24 PA15 25 PB3 26 PB4 27 PB5 28 PB6 29 PB7 30 PH3 31 R24

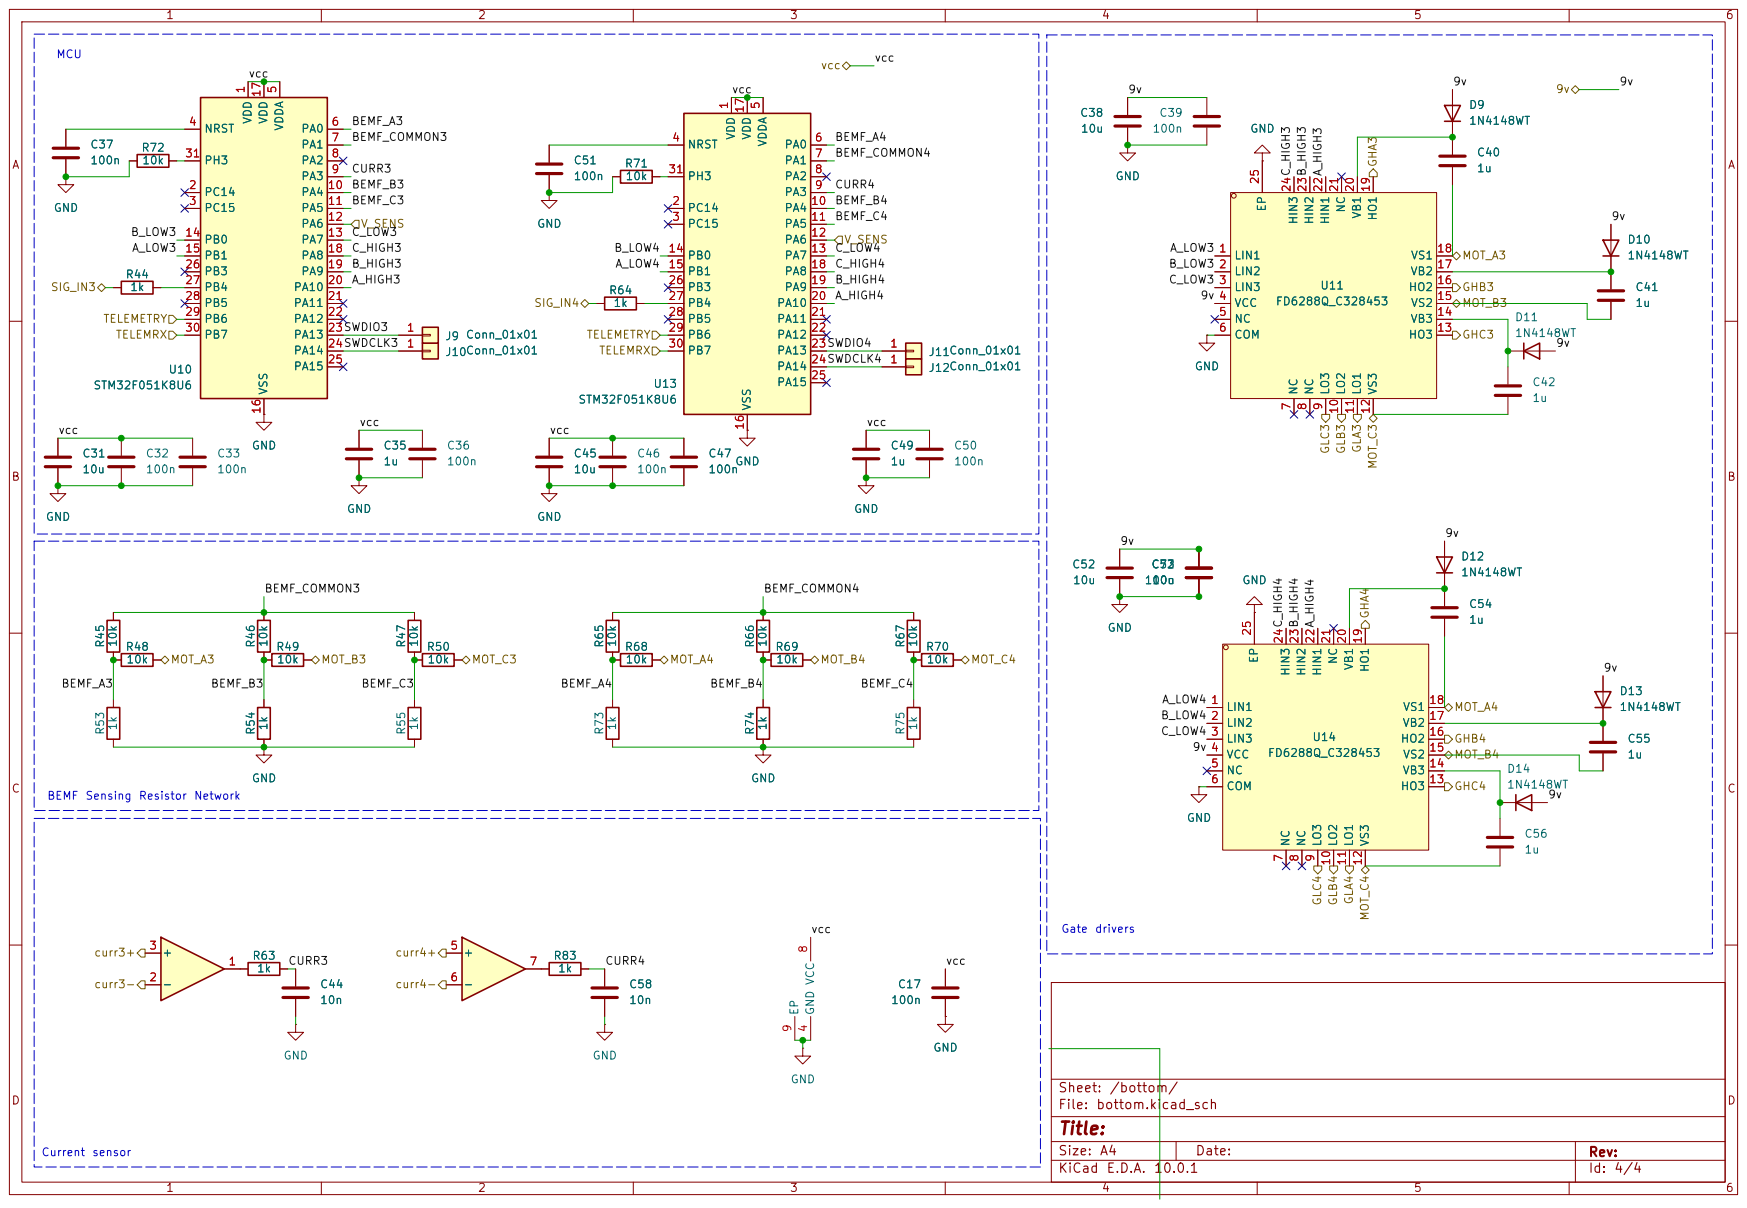
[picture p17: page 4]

1 PC14 2 PC15 3 NRST 4 VDDA 5 PA0 6 PA1 7 PA2 8 PA3 9 PA4 10 PA5 11 PA6 12 PA7 13 PB0 14 PB1 15 VSS 16 VDD 17 PA8 18 PA9 19 PA10 20 PA11 21 PA12 22 PA13 23 PA14 24 PA15 25 PB3 26 PB4 27 PB5 28 PB6 29 PB7 30 PH3 31 C37

1 PC14 2 PC15 3 NRST 4 VDDA 5 PA0 6 PA1 7 PA2 8 PA3 9 PA4 10 PA5 11 PA6 12 PA7 13 PB0 14 PB1 15 VSS 16 VDD 17 PA8 18 PA9 19 PA10 20 PA11 21 PA12 22 PA13 23 PA14 24 PA15 25 PB3 26 PB4 27 PB5 28 PB6 29 PB7 30 PH3 31 U10

1 PC14 2 PC15 3 NRST 4 VDDA 5 PA0 6 PA1 7 PA2 8 PA3 9 PA4 10 PA5 11 PA6 12 PA7 13 PB0 14 PB1 15 VSS 16 VDD 17 PA8 18 PA9 19 PA10 20 PA11 21 PA12 22 PA13 23 PA14 24 PA15 25 PB3 26 PB4 27 PB5 28 PB6 29 PB7 30 PH3 31 R64

1 PC14 2 PC15 3 NRST 4 VDDA 5 PA0 6 PA1 7 PA2 8 PA3 9 PA4 10 PA5 11 PA6 12 PA7 13 PB0 14 PB1 15 VSS 16 VDD 17 PA8 18 PA9 19 PA10 20 PA11 21 PA12 22 PA13 23 PA14 24 PA15 25 PB3 26 PB4 27 PB5 28 PB6 29 PB7 30 PH3 31 U13

File: bottom.kicad_sch | D Date:
Title:

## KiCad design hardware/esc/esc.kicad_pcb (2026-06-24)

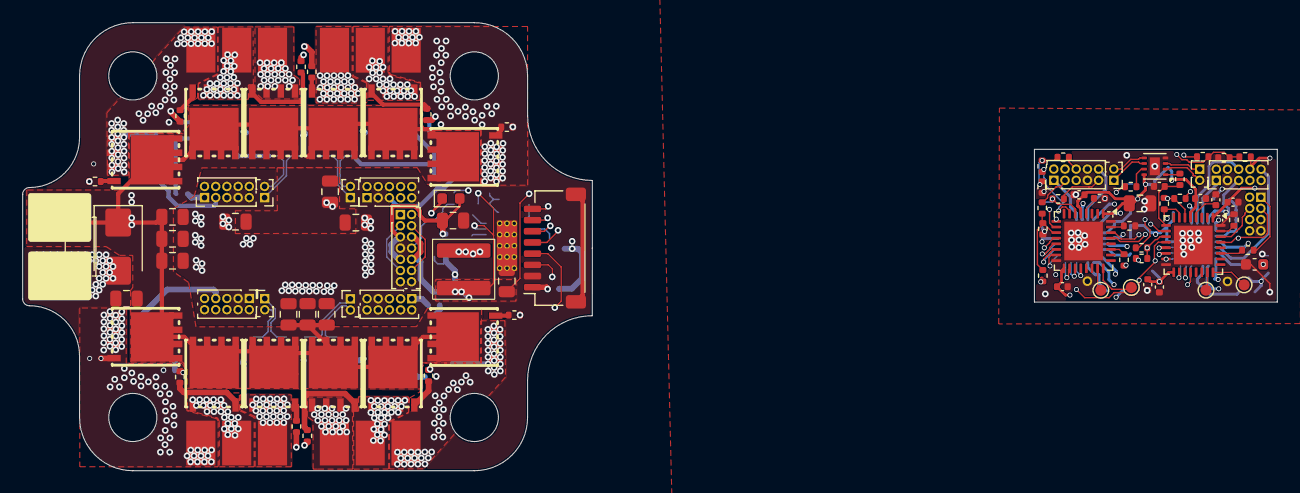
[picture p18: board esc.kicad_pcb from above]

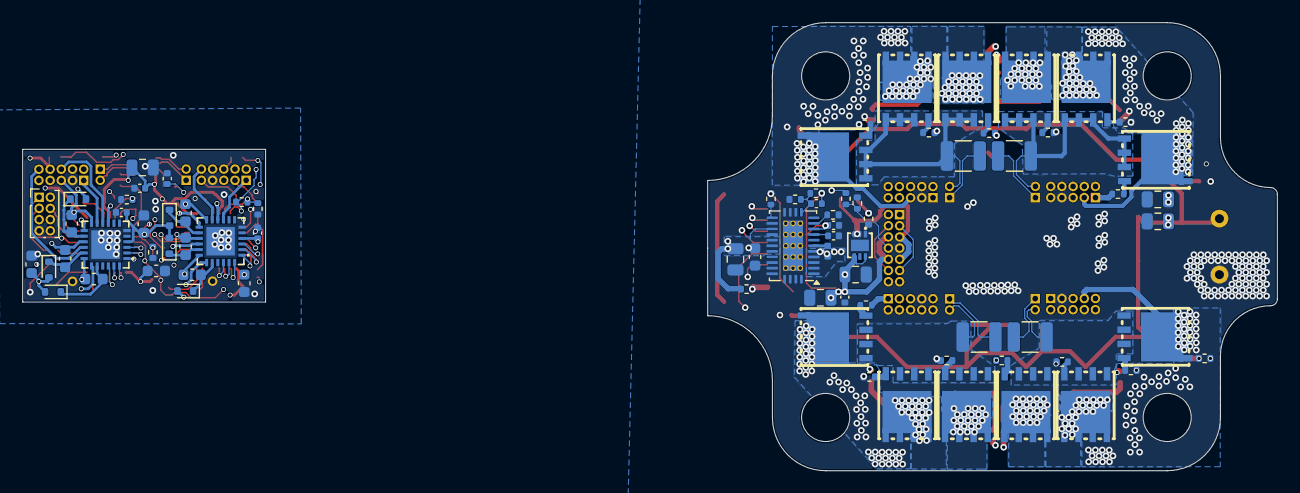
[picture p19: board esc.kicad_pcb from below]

Board: 6 copper layers, 112.0 x 40.0 mm, 173 parts (78 on the bottom side), 154 nets.

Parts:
C15, C20, C31, C34, C45, C59, C60, C61, C62, C63, C64, C65, C66, C67, C68, C69, C70, C78, C79: 10u; C_0805_2012Metric
C16: 470n; C_0402_1005Metric
C17, C32, C33, C36, C37, C39, C46, C47, C50, C51, C53, C75: 100n; C_0402_1005Metric
C35, C40, C41, C42, C49, C54, C55, C56: 1u; C_0603_1608Metric
C38, C52, C72: 10u; C_0603_1608Metric
C44, C58: 10n; C_0402_1005Metric
C71: C_Polarized; C_Disc_D5.0mm_W2.5mm_P5.00mm
C73: 1u; C_0402_1005Metric
C74: 2.2u; C_0402_1005Metric
C76: 2.2u; C_0603_1608Metric
C77: 5.1p; C_0402_1005Metric
D5: LED; D_0603_1608Metric
D9, D10, D11, D12, D13, D14: 1N4148WT; D_SOD-523
D15: SMBJ28A; D_SMB
J1, J2, J3, J21: Conn_01x03; Phase_Pads
J4: Conn_01x08_MountingPin; JST_SH_SM08B-SRSS-TB_1x08-1MP_P1.00mm_Horizontal
J9, J10, J11, J12: Conn_01x01; TestPoint_Pad_D1.0mm
J13, J14, J19, J20, J27, J28: Conn_02x05_Odd_Even; PinHeader_2x05_P1.00mm_Vertical
J15: Conn_02x07_Odd_Even; PinHeader_2x07_P1.00mm_Vertical
J16, J17, J18, J22, J25, J26: Conn_01x02; PinHeader_1x02_P1.00mm_Vertical
J29: Conn_02x04_Odd_Even; PinHeader_2x04_P1.00mm_Vertical
L1: 100u; inductor FANGCHENG FC-ALX 5050D-150MT
Q1, Q2, Q3, Q4, Q5, Q6, Q7, Q8, Q9, Q10, Q11, Q12, Q13, Q14, Q15, Q16, Q17, Q18, Q19, Q20, Q21, Q22, Q23, Q24: RS60N80UHG; DFN-8_L5.8-W4.9-P1.27-LS6.0-BL-1
R2, R42, R62, R82: 1mr; R_1210_3225Metric
R4, R5, R6, R7, R8, R9, R36, R37, R38, R39, R40, R41, R56, R57, R58, R59, R60, R61, R76, R77, R78, R79, R80, R81: 20r; R_0402_1005Metric
R10, R21: 100k; R_0402_1005Metric
R11: 12.4k; R_0402_1005Metric
R22, R45, R46, R47, R48, R49, R50, R65, R66, R67, R68, R69, R70, R71, R72: 10k; R_0402_1005Metric
R23, R44, R53, R54, R55, R63, R64, R73, R74, R75, R83: 1k; R_0402_1005Metric
R31: 0r; R_0402_1005Metric
R32: 105k; R_0402_1005Metric
R51: 36.5k; R_0402_1005Metric
U4: LM76003/2; Texas_RNP0030B_WQFN-30-1EP_4x6mm_P0.5mm_EP1.8x4.5mm_Thermal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
U5: LDL212PV33R; DFN-6_L2.0-W2.0-P0.50-BL-EP1.45
U6: INA2180A1; WSON-8-1EP_2x2mm_P0.5mm_EP0.9x1.6mm
U10, U13: STM32F051K8U6; QFN-32-1EP_5x5mm_P0.5mm_EP3.45x3.45mm
U11, U14: FD6288Q_C328453; QFN-24_L4.0-W4.0-P0.50-BL-EP2.6

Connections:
+9V: C20.1, C38.1, C39.2, C52.1, C53.2, C72.1, C73.1, C75.1, C77.2, C78.1, C79.1, D9.2 (A), D10.2 (A), D11.2 (A), D12.2 (A), D13.2 (A), D14.2 (A), J15.6, J15.10, J29.6, L1.2, R10.2, R32.1, U4.9 (BIAS), U5.4 (VIN), U5.6 (EN), U11.4 (VCC), U14.4 (VCC)
+BATT: C15.1, C59.1, C60.1, C61.1, C62.1, C63.1, C64.1, C65.1, C66.1, C67.1, C68.1, C69.1, C70.1, C71.1, C76.1, D15.1 (A1), Q1.D, Q3.D, Q5.D, Q7.D, Q8.D, Q9.D, Q13.D, Q14.D, Q15.D, Q19.D, Q20.D, Q21.D, R21.2, R31.1, U4.18 (EN), U4.20 (PVIN), U4.21 (PVIN), U4.22 (PVIN)
/Powerstage/GHA1: J27.10, R4.2
/Powerstage/GHA2: J28.4, R36.2
/Powerstage/GHA3: J19.2, R56.2
/Powerstage/GHA4: J20.8, R76.2
/Powerstage/GHB1: J27.2, R6.2
/Powerstage/GHB2: J28.8, R37.2
/Powerstage/GHB3: J19.10, R57.2
/Powerstage/GHB4: J20.4, R77.2
/Powerstage/GHC1: J27.3, R8.2
/Powerstage/GHC2: J28.5, R38.2
/Powerstage/GHC3: J19.7, R58.2
/Powerstage/GHC4: J20.5, R78.2
/Powerstage/GLA1: J27.9, R5.2
/Powerstage/GLA2: J28.2, R39.2
/Powerstage/GLA3: J19.1, R59.2
/Powerstage/GLA4: J20.10, R79.2
/Powerstage/GLB1: J27.6, R7.2
/Powerstage/GLB2: J28.10, R40.2
/Powerstage/GLB3: J19.6, R60.2
/Powerstage/GLB4: J20.2, R80.2
/Powerstage/GLC1: J27.1, R9.2
/Powerstage/GLC2: J28.9, R41.2
/Powerstage/GLC3: J19.9, R61.2
/Powerstage/GLC4: J20.1, R81.2
/Powerstage/MOT_A1: J21.1, J27.8, Q1.S, Q2.D
/Powerstage/MOT_A2: J1.1, J28.1, Q7.S, Q10.D
/Powerstage/MOT_A3: J2.1, J19.4, Q13.S, Q16.D
/Powerstage/MOT_A4: J3.1, J20.9, Q19.S, Q22.D
/Powerstage/MOT_B1: J21.2, J27.4, Q3.S, Q4.D
/Powerstage/MOT_B2: J1.2, J28.6, Q8.S, Q11.D
/Powerstage/MOT_B3: J2.2, J19.8, Q14.S, Q17.D
/Powerstage/MOT_B4: J3.2, J20.6, Q20.S, Q23.D
/Powerstage/MOT_C1: J21.3, J27.5, Q5.S, Q6.D
/Powerstage/MOT_C2: J1.3, J28.7, Q9.S, Q12.D
/Powerstage/MOT_C3: J2.3, J19.5, Q15.S, Q18.D
/Powerstage/MOT_C4: J3.3, J20.3, Q21.S, Q24.D
/Powerstage/SIG_IN1: J4.5, J15.13
/Powerstage/SIG_IN2: J4.6, J15.14
/Powerstage/SIG_IN3: J4.7, J15.2
/Powerstage/SIG_IN4: J4.8, J15.1
/Powerstage/TELEMETRY: J4.4, J15.3, J15.11
/Powerstage/TELEMRX: J4.3, J15.4, J15.12
/Powerstage/V_SENS: J15.8, R21.1, R22.2
/Powerstage/curr1+: J22.2, Q2.S, Q4.S, Q6.S, R2.1
/Powerstage/curr1-: J22.1, R2.2
/Powerstage/curr2+: J18.2, Q10.S, Q11.S, Q12.S, R42.1
/Powerstage/curr2-: J18.1, R42.2
/Powerstage/curr3+: J16.2, Q16.S, Q17.S, Q18.S, R62.1
/Powerstage/curr3-: J16.1, R62.2
/Powerstage/curr4+: J17.2, Q22.S, Q23.S, Q24.S, R82.1
/Powerstage/curr4-: J17.1, R82.2
/bottom/A_HIGH3: U10.20 (PA10), U11.22 (HIN1)
/bottom/A_HIGH4: U13.20 (PA10), U14.22 (HIN1)
/bottom/A_LOW3: U10.15 (PB1), U11.1 (LIN1)
/bottom/A_LOW4: U13.15 (PB1), U14.1 (LIN1)
/bottom/BEMF_A3: R45.1, R48.1, R53.2, U10.6 (PA0)
/bottom/BEMF_A4: R65.1, R68.1, R73.2, U13.6 (PA0)
/bottom/BEMF_B3: R46.1, R49.1, R54.2, U10.10 (PA4)
/bottom/BEMF_B4: R66.1, R69.1, R74.2, U13.10 (PA4)
/bottom/BEMF_C3: R47.1, R50.1, R55.2, U10.11 (PA5)
/bottom/BEMF_C4: R67.1, R70.1, R75.2, U13.11 (PA5)
/bottom/BEMF_COMMON3: R45.2, R46.2, R47.2, U10.7 (PA1)
/bottom/BEMF_COMMON4: R65.2, R66.2, R67.2, U13.7 (PA1)
/bottom/B_HIGH3: U10.19 (PA9), U11.23 (HIN2)
/bottom/B_HIGH4: U13.19 (PA9), U14.23 (HIN2)
/bottom/B_LOW3: U10.14 (PB0), U11.2 (LIN2)
/bottom/B_LOW4: U13.14 (PB0), U14.2 (LIN2)
/bottom/CURR3: C44.1, R63.2, U10.9 (PA3)
/bottom/CURR4: C58.1, R83.2, U13.9 (PA3)
/bottom/C_HIGH3: U10.18 (PA8), U11.24 (HIN3)
/bottom/C_HIGH4: U13.18 (PA8), U14.24 (HIN3)
/bottom/C_LOW3: U10.13 (PA7), U11.3 (LIN3)
/bottom/C_LOW4: U13.13 (PA7), U14.3 (LIN3)
/bottom/GHA3: J14.2, U11.19 (HO1)
/bottom/GHA4: J13.8, U14.19 (HO1)
/bottom/GHB3: J14.10, U11.16 (HO2)
/bottom/GHB4: J13.4, U14.16 (HO2)
/bottom/GHC3: J14.7, U11.13 (HO3)
/bottom/GHC4: J13.5, U14.13 (HO3)
/bottom/GLA3: J14.1, U11.11 (LO1)
/bottom/GLA4: J13.10, U14.11 (LO1)
/bottom/GLB3: J14.6, U11.10 (LO2)
/bottom/GLB4: J13.2, U14.10 (LO2)
/bottom/GLC3: J14.9, U11.9 (LO3)
/bottom/GLC4: J13.1, U14.9 (LO3)
/bottom/MOT_A3: C40.1, J14.4, R48.2, U11.18 (VS1)
/bottom/MOT_A4: C54.1, J13.9, R68.2, U14.18 (VS1)
/bottom/MOT_B3: C41.1, J14.8, R49.2, U11.15 (VS2)
/bottom/MOT_B4: C55.1, J13.6, R69.2, U14.15 (VS2)
/bottom/MOT_C3: C42.1, J14.5, R50.2, U11.12 (VS3)
/bottom/MOT_C4: C56.1, J13.3, R70.2, U14.12 (VS3)
/bottom/SIG_IN3: J29.1, R44.1
/bottom/SIG_IN4: J29.2, R64.1
/bottom/SWDCLK3: J10.1 (Pin_1_1), U10.24 (PA14)
/bottom/SWDCLK4: J12.1 (Pin_1_1), U13.24 (PA14)
/bottom/SWDIO3: J9.1 (Pin_1_1), U10.23 (PA13)
/bottom/SWDIO4: J11.1 (Pin_1_1), U13.23 (PA13)
/bottom/TELEMETRY: J29.3, U10.29 (PB6), U13.29 (PB6)
/bottom/TELEMRX: J29.4, U10.30 (PB7), U13.30 (PB7)
/bottom/V_SENS: J29.8, U10.12 (PA6), U13.12 (PA6)
/bottom/curr3+: J26.1, U6.3 (+)
/bottom/curr3-: J26.2, U6.2 (-)
/bottom/curr4+: J25.2, U6.5 (+)
/bottom/curr4-: J25.1, U6.6 (-)
GND: C15.2, C17.2, C20.2, C31.2, C32.2, C33.2, C34.2, C35.2, C36.2, C37.2, C38.2, C39.1, C44.2, C45.2, C46.2, C47.2, C49.2, C50.2, C51.2, C52.2, C53.1, C58.2, C59.2, C60.2, C61.2, C62.2, C63.2, C64.2, C65.2, C66.2, C67.2, C68.2, C69.2, C70.2, C71.2, C72.2, C73.2, C74.2, C75.2, C76.2, C78.2, C79.2, D15.2 (A2), J4.2, J4.MP (MountPin), J13.7, J14.3, J15.7, J19.3, J20.7, J27.7, J28.3, J29.7, R11.1, R22.1, R23.2, R51.2, R53.1, R54.1, R55.1, R71.1, R72.1, R73.1, R74.1, R75.1, U4.13 (AGND), U4.14 (AGND), U4.15 (AGND), U4.17 (SYNC/MODE), U4.19 (NC_{GND}), U4.24 (PGND), U4.25 (PGND), U4.26 (PGND), U4.27 (NC_{GND}), U4.28 (NC_{GND}), U4.29 (NC_{GND}), U4.30 (NC_{GND}), U4.31 (AGND), U5.1 (GND), U5.7 (EP), U6.4 (GND), U6.9 (EP), U10.16 (VSS), U10.32 (VSS), U10.33 (VSS), U11.6 (COM), U11.25 (EP), U13.16 (VSS), U13.32 (VSS), U13.33 (VSS), U14.6 (COM), U14.25 (EP)
unnamed: C16.2, L1.1, U4.1 (SW), U4.2 (SW), U4.3 (SW), U4.4 (SW), U4.5 (SW)
unnamed: D5.1 (K), R23.1
unnamed: C40.2, D9.1 (K), U11.20 (VB1)
unnamed: C41.2, D10.1 (K), U11.17 (VB2)
unnamed: C42.2, D11.1 (K), U11.14 (VB3)
unnamed: C54.2, D12.1 (K), U14.20 (VB1)
unnamed: C55.2, D13.1 (K), U14.17 (VB2)
unnamed: C56.2, D14.1 (K), U14.14 (VB3)
unnamed: J4.1, R31.2
unnamed: Q1.G, R4.1
unnamed: Q2.G, R5.1
unnamed: Q3.G, R6.1
unnamed: Q4.G, R7.1
unnamed: Q5.G, R8.1
unnamed: Q6.G, R9.1
unnamed: Q7.G, R36.1
unnamed: Q8.G, R37.1
unnamed: Q9.G, R38.1
unnamed: Q10.G, R39.1
unnamed: Q11.G, R40.1
unnamed: Q12.G, R41.1
unnamed: Q13.G, R56.1
unnamed: Q14.G, R57.1
unnamed: Q15.G, R58.1
unnamed: Q16.G, R59.1
unnamed: Q17.G, R60.1
unnamed: Q18.G, R61.1
unnamed: Q19.G, R76.1
unnamed: Q20.G, R77.1
unnamed: Q21.G, R78.1
unnamed: Q22.G, R79.1
unnamed: Q23.G, R80.1
unnamed: Q24.G, R81.1
unnamed: R63.1, U6.1
unnamed: R83.1, U6.7
unnamed: C16.1, U4.6 (BOOT)
unnamed: C77.1, R10.1, R11.2, U4.12 (FB)
unnamed: R32.2, U4.16 (PGOOD)
unnamed: R51.1, U4.10 (RT)
unnamed: C74.1, U4.8 (VCC)
unnamed: C37.1, U10.4 (NRST)
unnamed: R44.2, U10.27 (PB4)
unnamed: R72.2, U10.31 (PH3)
unnamed: C51.1, U13.4 (NRST)
unnamed: R64.2, U13.27 (PB4)
unnamed: R71.2, U13.31 (PH3)
VCC: C17.1, C31.1, C32.1, C33.1, C34.1, C35.1, C36.1, C45.1, C46.1, C47.1, C49.1, C50.1, D5.2 (A), J15.5, J15.9, J29.5, U5.2 (ADJ/sense), U5.3 (VOUT), U6.8 (VCC), U10.1 (VDD), U10.5 (VDDA), U10.17 (VDD), U13.1 (VDD), U13.5 (VDDA), U13.17 (VDD)

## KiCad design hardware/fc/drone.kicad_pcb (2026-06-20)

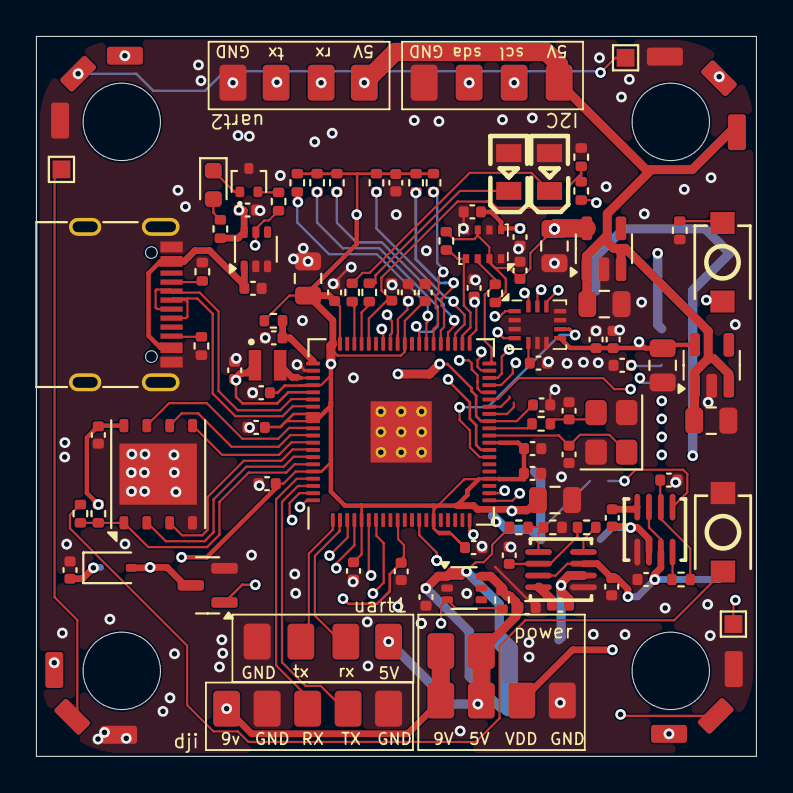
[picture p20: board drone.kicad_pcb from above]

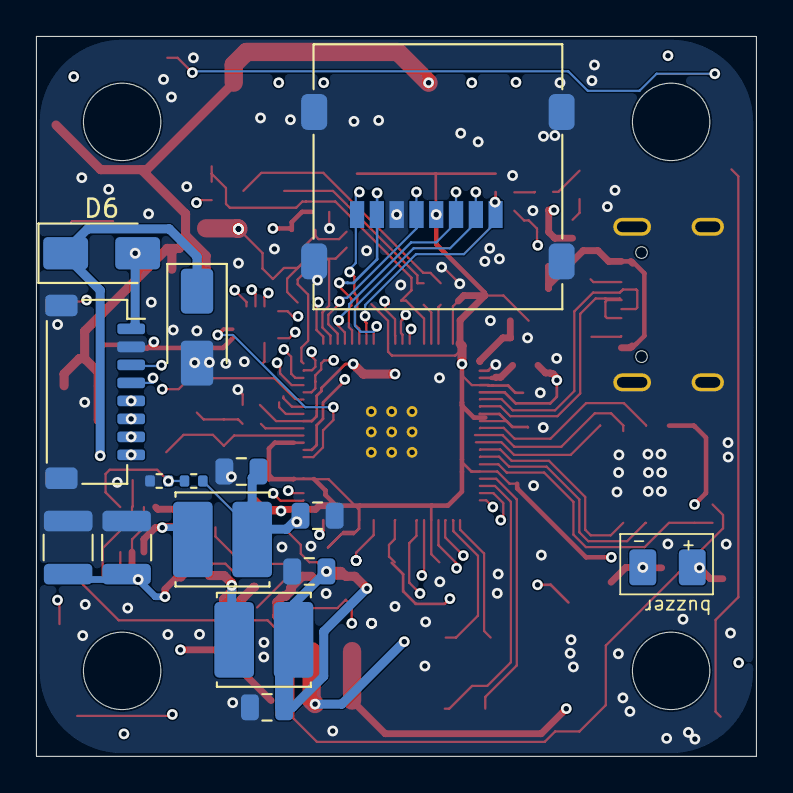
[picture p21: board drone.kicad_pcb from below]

Board: 4 copper layers, 40.0 x 40.0 mm, 137 parts (16 on the bottom side), 82 nets.

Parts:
C1, C4, C5, C6, C11, C12, C15, C16, C21, C22, C25, C26, C29, C35, C37, C38, C41, C42, C43, C45, C46, C49, C51: 100nf; C_0402_1005Metric
C2, C3, C7, C31: 4.7u; C_0402_1005Metric
C8, C17, C33: 100n; C_0402_1005Metric
C9, C10: 15p; C_0402_1005Metric
C13, C14, C23, C24: 1uf; C_0805_2012Metric
C18, C20, C30, C36: 22u; C_0805_2012Metric
C19, C34: 10u; C_1210_3225Metric
C27, C47: 2.2uf; C_0402_1005Metric
C28, C32, C39, C40: 1uf; C_0402_1005Metric
C44, C48: 10uf; C_0805_2012Metric
D1: C2297; LED0805-R-RD
D2: LED; LED_0603_1608Metric
D3: C2296; LED0805-R-RD
D4: D_Schottky; D_SOD-323
D6: D_Schottky; D_SMA
D8: SMAJ30A; D_SMA
J1, J3, J4, J5, J6, J7, J8, J9, J10, J11, J13, J14, J15, J16, J17, J18, J23, J24, J25, J26, J27, J28, J29: Conn_01x01; signal_pad
J2: Conn_01x08; JST_SH_SM08B-SRSS-TB_1x08-1MP_P1.00mm_Horizontal
J12: Micro_SD_Card; microSD_HC_Molex_47219-2001
J19, J20, J21, J22: Conn_01x03; led_ring
J30, J31, J32: Conn_01x01; TestPoint_Pad_1.0x1.0mm
L1, L2: 22uH; L_Cenker_CKCS5040
L3: 3.3u; L_pol_2016
Q1: AO3400A; SOT-23
Q2: NPN; SOT-416
R1, R2, R3, R4, R13, R20, R22, R23, R24, R27, R28, R29, R30: 10k; R_0402_1005Metric
R5, R7, R9, R10, R12: 100k; R_0402_1005Metric
R6, R14: 24.9k; R_0402_1005Metric
R8: 33r; R_0402_1005Metric
R11, R19, R21, R26: 1k; R_0402_1005Metric
R15, R16: 5.1k; R_0402_1005Metric
R25: 0; R_0402_1005Metric
SW1, SW2: SW_Push; SW-SMD_L3.9-W3.0-P4.45
TP1: BUZZER+; signal_pad
TP2: BUZZER-; signal_pad
U1, U7: MP9943GQ(TOKMAS); QFN-8_L3.0-W3.0-P0.65-BL
U2: TLV75533PDBV; SOT-23-5
U3: W25Q128JVP; WSON-8-1EP_6x5mm_P1.27mm_EP3.4x4.3mm
U4: RP2350_80QFN; RP2350-QFN-80-1EP_10x10_P0.4mm_EP3.4x3.4mm_ThermalVias
U5: ICM-42688-P; Bosch_LGA-14_3x2.5mm_P0.5mm
U6: LP5907MFX-3.3; SOT-23-5
U8: BMP280; Bosch_LGA-8_2x2.5mm_P0.65mm_ClockwisePinNumbering
U9, U10: LM66100DCK; SOT-363_SC-70-6
USB1: USB_C_Receptacle_USB2.0_14P; USB_C_Receptacle_G-Switch_GT-USB-7010ASV
Y1: ABM8-272-T3; Crystal_SMD_3225-4Pin_3.2x2.5mm

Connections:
+1V1: C2.1, C8.1, C11.2, C31.1, L3.1, U4.10 (DVDD), U4.32 (DVDD), U4.51 (DVDD), U4.65 (VREG_FB)
+5V: C14.1, C16.2, C23.2, C38.1, C41.1, D4.1 (K), J3.1 (Pin_1_1), J11.1 (Pin_1_1), J13.1 (Pin_1_1), J19.3, J20.3, J21.3, J22.3, J24.1 (Pin_1_1), J29.1 (Pin_1_1), R3.2, R11.1, TP1.1 (1_1), U2.1 (IN), U2.3 (EN), U6.1 (IN), U6.3 (EN), U9.6 (VOUT), U10.6 (VOUT)
+9V: C30.1, C36.1, J5.1 (Pin_1_1), J10.1 (Pin_1_1), J23.1 (Pin_1_1), L2.2, R9.2
/QSPI_SCLK: U3.6 (CLK), U4.71 (QSPI_SCLK)
/QSPI_SD0: U3.5 (DI/IO_{0}), U4.72 (QSPI_SD0)
/QSPI_SD1: U3.2 (DO/IO_{1}), U4.74 (QSPI_SD1)
/QSPI_SD2: U3.3 (~WP/IO_{2}), U4.73 (QSPI_SD2)
/QSPI_SD3: U3.7 (~HOLD/~RESET/IO_{3}), U4.70 (QSPI_SD3)
/QSPI_SS: R1.2, R25.2, U3.1 (~CS), U4.75 (QSPI_SS)
/VREG_AVDD: C3.1, R8.2, U4.61 (VREG_AVDD)
/VREG_LX: L3.2, U4.63 (VREG_LX)
/XIN: C10.1, U4.30 (XIN), Y1.1
/XOUT: R26.1, U4.31 (XOUT)
/~USB_BOOT: R1.1, SW1.2
BAT_CURR: C22.2, J2.3 (Current), U4.52 (GPIO41_ADC1)
BAT_POWER: D6.2 (A), J2.1 (Power), R12.2
BAT_POW_PROT: C17.2, C19.1, C33.2, C34.1, D6.1 (K), D8.1 (A1), U1.3 (EN), U1.7 (VIN), U7.3 (EN), U7.7 (VIN)
BAT_VOLTAGE: C21.1, R12.1, R13.2, U4.55 (GPIO44_ADC4)
CMD: J12.3 (CMD), R23.2, U4.44 (GPIO35)
DAT0: J12.7 (DAT0), R27.2, U4.45 (GPIO36)
DAT1: J12.8 (DAT1), R28.2, U4.46 (GPIO37)
DAT2: J12.1 (DAT2), R20.2, U4.47 (GPIO38)
DAT3: J12.2 (DAT3/CD), R22.2, U4.48 (GPIO39)
DJI_RX0: J16.1 (Pin_1_1), U4.77 (GPIO0)
DJI_TX0: J17.1 (Pin_1_1), U4.78 (GPIO1)
GND: C1.2, C2.2, C3.2, C4.2, C5.2, C6.2, C7.2, C8.2, C9.2, C10.2, C11.1, C12.2, C13.2, C14.2, C15.1, C16.1, C17.1, C18.2, C19.2, C20.2, C21.2, C22.1, C23.1, C24.1, C25.2, C26.2, C27.2, C28.2, C30.2, C31.2, C32.2, C33.1, C34.2, C36.2, C37.2, C38.2, C39.1, C40.2, C41.2, C42.2, C43.2, C44.2, C45.2, C46.2, C47.2, C48.2, C49.2, C51.2, D1.1 (K), D3.1 (K), D8.2 (A2), J1.1 (Pin_1_1), J2.2 (Ground), J4.1 (Pin_1_1), J12.6 (VSS), J12.9 (SHIELD), J14.1 (Pin_1_1), J15.1 (Pin_1_1), J18.1 (Pin_1_1), J19.1, J20.1, J21.1, J22.1, J28.1 (Pin_1_1), Q1.2 (S), Q2.3 (E), R2.1, R6.1, R13.1, R14.1, R15.2, R16.1, SW1.1, U1.5 (GND), U2.2 (GND), U3.4 (GND), U3.9 (EP), U4.62 (VREG_PGND), U4.81 (GND), U5.2 (RESV), U5.3 (RESV), U5.6 (GND), U5.7 (RESV), U5.10 (RESV), U5.11 (RESV), U6.2 (GND), U7.5 (GND), U8.1 (GND), U8.5 (SDO), U8.7 (GND), U9.2 (GND), U9.3 (~CE), U10.2 (GND), USB1.A1 (GND), USB1.A12 (GND), USB1.B1 (GND), USB1.B12 (GND), USB1.S1 (SHIELD), Y1.2, Y1.4
I2C1_SCL: J27.1 (Pin_1_1), U4.80 (GPIO3)
I2C1_SDA: J26.1 (Pin_1_1), U4.79 (GPIO2)
I2C_SCK: R30.1, U4.42 (GPIO33), U8.4 (SCK)
I2C_SDA: R29.1, U4.40 (GPIO32), U8.3 (SDI)
IMU_CLK: U4.38 (GPIO30), U5.13 (AP_SCL/AP_SCLK)
IMU_CLKIN: U4.27 (GPIO26), U5.9 (INT2/FSYNC/CLKIN)
IMU_CS: U4.37 (GPIO29), U5.12 (AP_CS)
IMU_INT: U4.28 (GPIO27), U5.4 (INT1/INT)
IMU_SDA: U4.39 (GPIO31), U5.14 (AP_SDA/AP_SDIO/AP_SDI)
IMU_SDO: U4.36 (GPIO28), U5.1 (AP_SDO/AP_AD0)
LED_1: J20.2, U4.13 (GPIO14)
LED_2: J21.2, J30.1 (Pin_1_1)
LED_3: J22.2, J31.1 (Pin_1_1)
LED_4: J19.2, J32.1 (Pin_1_1)
LIPO_5V: C18.1, C20.1, C40.1, L1.2, R5.2, U10.1 (VIN)
MOTOR_1: J2.5 (Motor_1), U4.3 (GPIO6)
MOTOR_2: J2.6 (Motor_2), U4.4 (GPIO7)
MOTOR_3: J2.7 (Motor_3), U4.6 (GPIO8)
MOTOR_4: J2.8 (Motor_4), U4.7 (GPIO9)
unnamed: C9.1, R26.2, Y1.3
unnamed: D1.2 (A), R21.1
unnamed: D2.2 (A), R11.2
unnamed: D2.1 (K), Q2.1 (C)
unnamed: D3.2 (A), R19.1
unnamed: D4.2 (A), Q1.3 (D), TP2.1 (1_1)
unnamed: Q2.2 (B), R4.2
unnamed: R2.2, SW2.1
unnamed: C29.1, U1.4 (BST)
unnamed: R5.1, R6.2, U1.1 (FB)
unnamed: R7.2, U1.8 (PG)
unnamed: C29.2, L1.1, U1.6 (SW)
unnamed: C28.1, R7.1, U1.2 (VCC)
unnamed: SW2.2, U4.35 (RUN)
unnamed: C35.1, U7.4 (BST)
unnamed: R9.1, R14.2, U7.1 (FB)
unnamed: R10.2, U7.8 (PG)
unnamed: C35.2, L2.1, U7.6 (SW)
unnamed: C32.1, R10.1, U7.2 (VCC)
unnamed: R3.1, R4.1, U9.5 (ST), U10.3 (~CE)
unnamed: R16.2, USB1.A5 (CC1)
unnamed: R15.1, USB1.B5 (CC2)
PIO_UART2_RX: J8.1 (Pin_1_1), U4.21 (GPIO21)
PIO_UART2_TX: J9.1 (Pin_1_1), U4.22 (GPIO22)
SD_CLK: J12.5 (CLK), R24.2, U4.43 (GPIO34)
TELEMETRY: J2.4 (Telemetry), U4.53 (GPIO42_ADC2)
USART1_RX: J6.1 (Pin_1_1), U4.2 (GPIO5)
USART1_TX: J7.1 (Pin_1_1), U4.1 (GPIO4)
USB_5V: C39.2, U9.1 (VIN), USB1.A4 (VBUS), USB1.A9 (VBUS), USB1.B4 (VBUS), USB1.B9 (VBUS)
USB_D+: U4.67 (USB_DP), USB1.A6 (D+), USB1.B6 (D+)
USB_D-: U4.66 (USB_DM), USB1.A7 (D-), USB1.B7 (D-)
VACC: C24.2, C25.1, C27.1, C46.1, C47.1, U5.8 (VDD), U6.5 (OUT), U8.8 (VDD)
VCC: C26.1, U5.5 (VDDIO)
VDD: C1.1, C4.1, C5.1, C6.1, C7.1, C12.1, C13.1, C15.2, C37.1, C42.1, C43.1, C44.1, C45.1, C48.1, C49.1, C51.1, J12.4 (VDD), J25.1 (Pin_1_1), R8.1, R20.1, R22.1, R23.1, R24.1, R25.1, R27.1, R28.1, R29.2, R30.2, U2.5 (OUT), U3.8 (VCC), U4.5 (IOVDD), U4.15 (IOVDD), U4.24 (IOVDD), U4.29 (IOVDD), U4.41 (IOVDD), U4.50 (IOVDD), U4.59 (ADC_AVDD), U4.60 (IOVDD), U4.64 (VREG_VIN), U4.68 (USB_OTP_VDD), U4.69 (QSPI_IOVDD), U4.76 (IOVDD), U8.2 (CSB), U8.6 (VDDIO)
buzz: Q1.1 (G), U4.20 (GPIO20)
green_led: R21.2, U4.56 (GPIO45_ADC5)
yellow_led: R19.2, U4.57 (GPIO46_ADC6)

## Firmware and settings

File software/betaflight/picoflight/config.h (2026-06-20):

/*
 * This file is part of Betaflight.
 *
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
 * See the GNU General Public License for more details.
 *
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
 * If not, see <http://www.gnu.org/licenses/>.
 * 
 * This file was copied from MADFLIGHT_FC3 config and edited to match with picoflight pinout
 */

#pragma once

#define FC_TARGET_MCU        RP2350B
#define BOARD_NAME           picoflight
#define MANUFACTURER_ID      pota //to

// Board info: https://madflight.com/Board-FC3/

// For debugging (trace) via UART, make with env var PICO_TRACE set (see RP2350.mk).
// Example instance and pins below.
//#define PICO_TRACE_UART_INSTANCE  0
//#define PICO_TRACE_TX_GPIO        20
//#define PICO_TRACE_RX_GPIO        21

//------------------
// Internal Pins
//------------------

// Bus for internal I2C sensors
// NOTE: Board has BMP580 barometer, MMC5603 compass and INA226 power sensor. Sensors not supported by betaflight_2025.12.0-beta
#define I2C0_SCL_PIN         PA33
#define I2C0_SDA_PIN         PA32

//bmp280 barometer
#define USE_BARO_BMP280
#define BARO_I2C_INSTANCE            I2C0

// LED
#define LED0_PIN             PA45 // blue
//#define LED0_INVERTED

// Battery voltage
#define USE_ADC
#define ADC_INSTANCE         ADC1
#define ADC_VBAT_PIN         PA44
#define DEFAULT_VOLTAGE_METER_SOURCE   VOLTAGE_METER_ADC
#define DEFAULT_VOLTAGE_METER_SCALE    110 // 100k/10k divider

// RGB LED
#define LED_STRIP_PIN        PA14

// Gyro+acc
#define USE_GYRO_CLKIN
#define USE_GYRO
#define USE_GYRO_SPI_ICM42688P
#define USE_ACC
#define USE_ACC_SPI_ICM42688P
#define USE_ACCGYRO_ICM45686
#define USE_ACCGYRO_LSM6DSO
#define USE_ACCGYRO_LSM6DSV16X
#define USE_SPI_DEVICE_1
#define SPI1_SCK_PIN         PA30
#define SPI1_SDI_PIN         PA28
#define SPI1_SDO_PIN         PA31
#define GYRO_1_EXTI_PIN      PA27
#define GYRO_1_CS_PIN        PA29
#define GYRO_1_CLKIN_PIN     PA26  // for ICM42688P,ICP45686 needs #define USE_GYRO_CLKIN
#define GYRO_1_SPI_INSTANCE  SPI1
#define GYRO_1_ALIGN         CW180_DEG

// SDCARD 1-bit SPI - works
#define USE_SDCARD
#define USE_SDCARD_SPI
#define SPI0_SCK_PIN         PA34
#define SPI0_SDI_PIN         PA36
#define SPI0_SDO_PIN         PA35
#define SDCARD_SPI_CS_PIN    PA39
#define SDCARD_DETECT_PIN    NONE
#define SDCARD_DETECT_INVERTED
#define SDCARD_SPI_INSTANCE  SPI0
#define DEFAULT_BLACKBOX_DEVICE        BLACKBOX_DEVICE_SDCARD

/*
// SDCARD 4-bit SDIO - TODO - Compiles but still have "SD-CARD: Not configured" in configurator with betaflight_2025.12.0-beta
#define USE_SDCARD
#define SDCARD_DETECT_PIN    NONE
#define SDIO_DEVICE          SDIODEV_1
#define SDIO_USE_4BIT        1
#define SDIO_CK_PIN          PA34
#define SDIO_CMD_PIN         PA35
#define SDIO_D0_PIN          PA36
#define SDIO_D1_PIN          PA37
#define SDIO_D2_PIN          PA38
#define SDIO_D3_PIN          PA39
#define DEFAULT_BLACKBOX_DEVICE        BLACKBOX_DEVICE_SDCARD
*/

//------------------
// External Pins
//------------------

// Board has 3 rows of 10 external GPIOS, each row has 3 power+ground pins. Available pins are PA0-25,40-43

// --- First row of pins ---

// RC Radio - 1-on-1 connect ELRS / CRSF module
#define UART0_TX_PIN         PA0
#define UART0_RX_PIN         PA1
//+5V
//GND

// GPS + Compass
#define I2C1_SDA_PIN         PA2
#define I2C1_SCL_PIN         PA3
#define UART1_TX_PIN         PA4
#define UART1_RX_PIN         PA5
//+5V
//GND

// Motors
#define MOTOR1_PIN           PA6 // pwm3a
#define MOTOR2_PIN           PA7 // pwm3b
#define MOTOR3_PIN           PA8 // pwm4a
#define MOTOR4_PIN           PA9 // pwm4b
//+3.3V
//GND

#define BEEPER_PIN           PA20

// --- Second row of pins ---

// Additional UART
#define PIOUART0_TX_PIN      PA21
#define PIOUART0_RX_PIN      PA22
//+5V
//GND

// External LEDs
//#define LED1_PIN             PA12 // green
//#define LED1_INVERTED
//#define LED2_PIN             PA13 // red
//#define LED2_INVERTED

// Additional UART
//#define PIOUART1_TX_PIN      PA14
//#define PIOUART1_RX_PIN      PA15
//+5V
//GND

// Additional motors
//#define MOTOR5_PIN           PA16 // pwm0a
//#define MOTOR6_PIN           PA17 // pwm0b
//#define MOTOR7_PIN           PA18 // pwm1a
//#define MOTOR8_PIN           PA19 // pwm1b
//+3.3V
//GND

// --- Third row of pins ---

// Debugging (trace) via UART
//PA20 used as PICO_TRACE_TX_GPIO
//PA21 used as PICO_TRACE_RX_GPIO
//+5V
//GND

// GPIOs
//#define PINIO1_PIN PA22
//#define PINIO2_PIN PA23
//#define PINIO3_PIN PA24
//#define PINIO4_PIN PA25
//+5V
//GND

// ADC pins
//#define ADC_RSSI_PIN         PA40
//#define ADC_CURR_PIN         PA41 //with this stack curr pin is replaced with telemrx
#define ADC_EXTERNAL1_PIN    PA42
//PA43 unused
//+3.3V
//GND

// Optional external barometer connected to I2C1 (second i2c bus) PA2=SDA PA3=SCL
#define USE_BARO
#define USE_BARO_MS5611
#define USE_BARO_BMP280
#define USE_BARO_BMP388
#define USE_BARO_LPS
#define USE_BARO_QMP6988
#define USE_BARO_DPS310
#define USE_BARO_BMP085
#define USE_BARO_2SMBP_02B
#define USE_BARO_LPS22DF
#define BARO_I2C_INSTANCE    I2CDEV_1

// Optional external compass connected to I2C1 (second i2c bus) PA2=SDA PA3=SCL
#define USE_MAG
#define USE_MAG_HMC5883
#define USE_MAG_QMC5883
#define USE_MAG_LIS2MDL
#define USE_MAG_LIS3MDL
#define USE_MAG_AK8975
#define USE_MAG_IST8310
#define MAG_I2C_INSTANCE     I2CDEV_1

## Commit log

2025-12-30 pcb update
    [drone.kicad_pcb, drone.kicad_sch]
2025-12-30 commit
    +gitignore
    +esc schematic
    [esc.kicad_pcb, esc.kicad_sch]
2025-12-31 update sch
    fixed wrong mcu package
    + i suppose gitignore doing its thing
    [esc.kicad_sch]
2026-01-02 finished routinnnn
    :3
    [drone.kicad_pcb, drone.kicad_sch]
2026-04-29 poush up to date
    its been a long time since i last pushed but some updates were on the way
    [RP2350_QFN80.step, drone.kicad_pcb, esc.kicad_pcb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]
2026-06-24 reorg+ fixes
    [BOM.csv, FLIGHT STACK.f3d, RP2350_QFN80.step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]

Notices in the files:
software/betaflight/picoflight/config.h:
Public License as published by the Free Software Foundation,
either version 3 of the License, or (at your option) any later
